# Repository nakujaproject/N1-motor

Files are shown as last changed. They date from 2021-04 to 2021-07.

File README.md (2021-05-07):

# N1-motor
`
 Reporsitory that holds files related to the N1 motor development for the Nakuja Project`

    

***
## Table of Contents

1. [Description](#description)
2. [Goals](#goals)
3. [Methodology](#methodology)
4. [Key Design Parameters](#key-design-parameters)
5. [Directories](#directories)
6. [Technologies](#technologies)

***

## Description

The N1 motor is a Solid Rocket Motor developed by the Nakuja Project. The motor is meant to be used on a small launch vehicle. The purpose of the motor is to offer propulsion to a rocket that will be recovered in so doing put into practise the skills of armature experimental rocketry

## Goals
The N1 motor is expected to propel the launch vehicle to a hieght of between `50 to  100m`

## Methodology
The motor is made up of one of three propellant combinations:
> + KNSU(Potassium Nitrate + Sucrose)
> + KNDX(Potassium Nitrate + Dextrose)
> + KNSB(Potassium Nitrate + Sorbitorl)

The three fuels are to be cast to form free standing grains which are to  be assembled in a pvc pipe along with a nozzle and endcaps.
This repo contains design, simulation data as well as results obtained from static tests conducted on different grains and parameters

## Key Design Parameters
The following factors are taken into consideration when designing the N1 motor:
- Performance- The motor must provide enough thrust to take the launch vehicle to a minimum of 50m
- Chamber Pressure - The chamber pressure must be within the workable range of the UPvc pipe we are currently using
- Rocket Airframe design-  the rocket must fit into the designed launch vehicle

## Directories
The following is a list of the contents of each directory in the reporsitory:
+ [Drawings](/Drawings) - contains all the design drawings for the N1 motor
+ [Proposed Final Spec](/Proposed%20Final%20Spec) -contains design simulations to obtain specifications for final motor
+ [Tests](/Tests) -contains all data obtained from static tests

## Technologies
The design and simulation of the N1 motor uses the following software:
1. SRM.xls obtained from the nakka rocketry website. Link attached [here](https://www.nakka-rocketry.net/soft/SRM_2014.1.zip)
2. openMotor- [Link](https://github.com/reilleya/openMotor)
3. OpenRocket - [Link](https://openrocket.info/)

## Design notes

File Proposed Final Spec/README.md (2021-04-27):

# Updated proposed N1-Motor
Grain Diameter 30mm \
Grain Length 150mm
performance | KNSU V6 | KNSU V7 | KNDX V8 | KNDX V9 
--- | --- | --- | --- | --- 
Designation | F87 | F92 | F65 | F63
Impulse | 67.07 | 66.91 | 70.37 | 72.65
Propellant mass (Kg) | 0.13 | 0.14 | 0.15 | 0.15
Average Pressure (MPa) | 1.45 | 1.80 | 1.87 | 1.83
Peak Pressure (MPa) | 1.89 | 2.40 | 2.33 | 2.31
Core (mm) | 17 | 16 | 14 | 13
Throat (mm) | 12 | 11 | 9 | 9
Burn Time (s) | 0.69 | 0.69 | 1.05 | 1.11
Rasp File | [ENG FILE](V6-KNSU/V6-KNSU.eng)| [ENG FILE](V7-KNSU/V7-KNSU.eng)| [ENG FILE](V8-KNDX/V8-KNDX.eng)| [ENG FILE](V8-KNDX/V8-KNDX.eng)
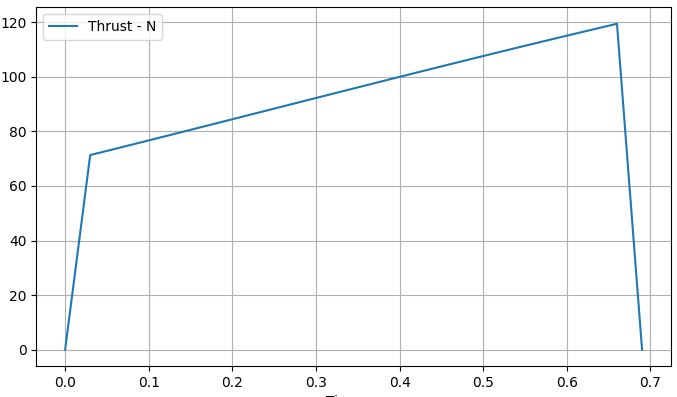
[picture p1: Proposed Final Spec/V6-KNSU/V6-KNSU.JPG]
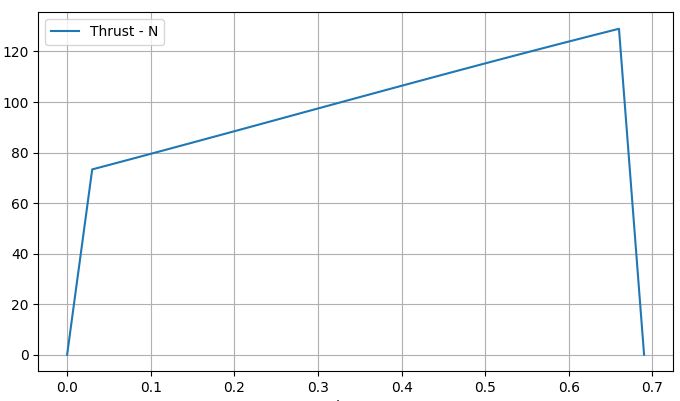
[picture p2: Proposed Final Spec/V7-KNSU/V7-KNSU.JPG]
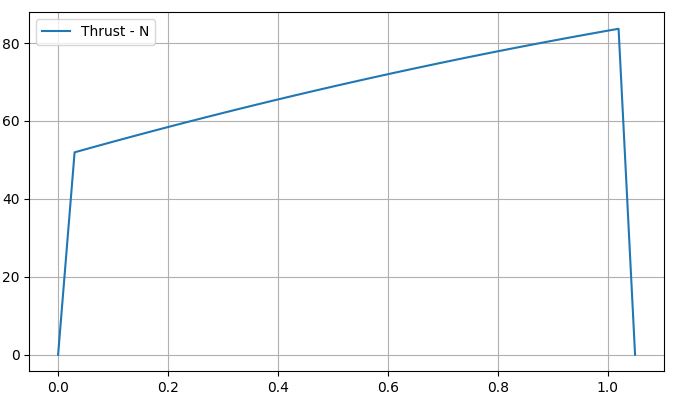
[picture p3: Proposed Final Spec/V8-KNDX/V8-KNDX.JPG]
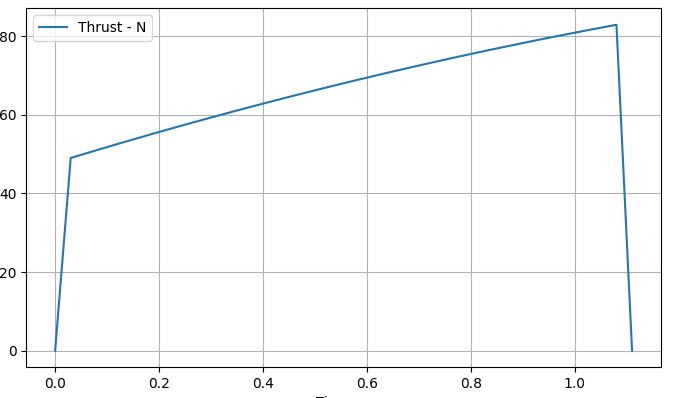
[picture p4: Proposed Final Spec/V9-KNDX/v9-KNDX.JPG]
Thrust Curve |  |  |  | 

# Motor selection
https://docs.google.com/spreadsheets/d/1xEjgxcizVEla5WYd4yQHLdHGN3GgNQR9PQ9QDNRd-24/edit?pli=1#gid=1338705104

# New motor specifications with nozzles

Grain Diameter 30mm \
Grain Length 130mm

performance | KNSU v10 | KNDX v11 | KNSB v12
--- | --- | --- | ---
Designation | G146 | G106 | G108
Impulse(Ns) | 109.61 | 115.36 | 110.36
Propellant mass (Kg) | 0.12 | 0.13 | 0.13
Average Pressure (MPa) | 1.46 | 1.46 | 1.48
Peak Pressure (MPa) | 1.89 | 1.79 | 1.79
Core (mm) | 16 | 14 | 14
Throat (mm) | 11 | 9.5 | 9.5
Burn Time (s) | 0.72 | 1.05 | 0.99
Rasp File | [ENG FILE](V10-KNSU/N1-V10-KNSU.eng) | [ENG FILE](V11-KNDX/N1-V11-KNDX.eng) | [ENG FILE](V12-KNSB/N1-V12-KNSB.eng)
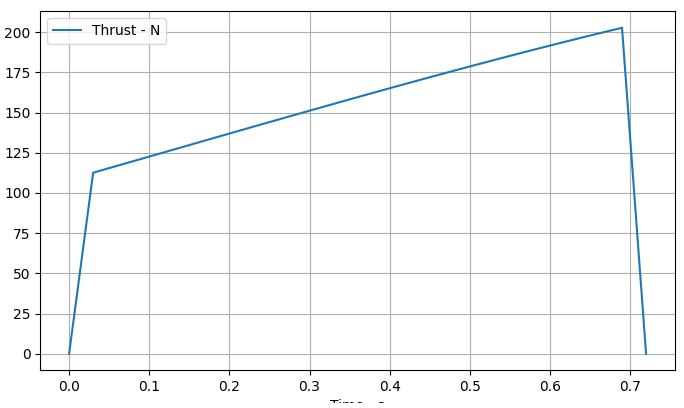
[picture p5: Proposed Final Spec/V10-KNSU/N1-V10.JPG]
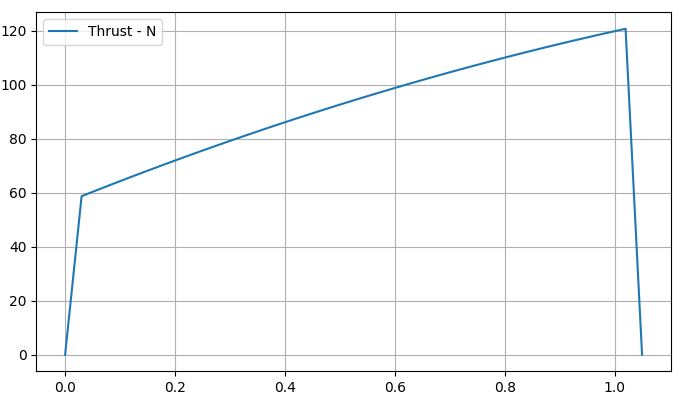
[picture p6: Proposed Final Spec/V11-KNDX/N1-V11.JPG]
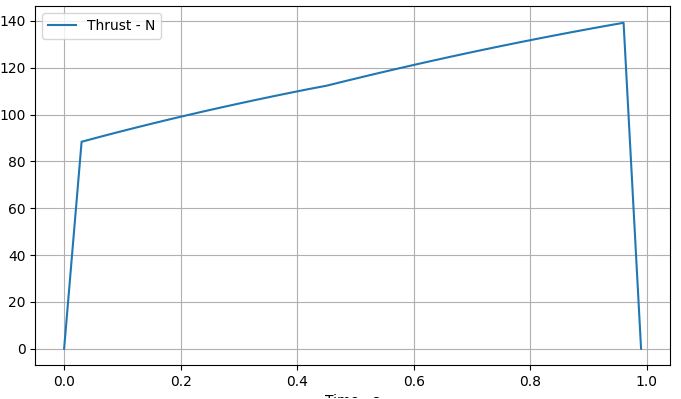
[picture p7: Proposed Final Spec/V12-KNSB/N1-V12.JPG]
Thrust Curve |  |  |

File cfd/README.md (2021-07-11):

# N1 Nozzle CFD
### Pressure
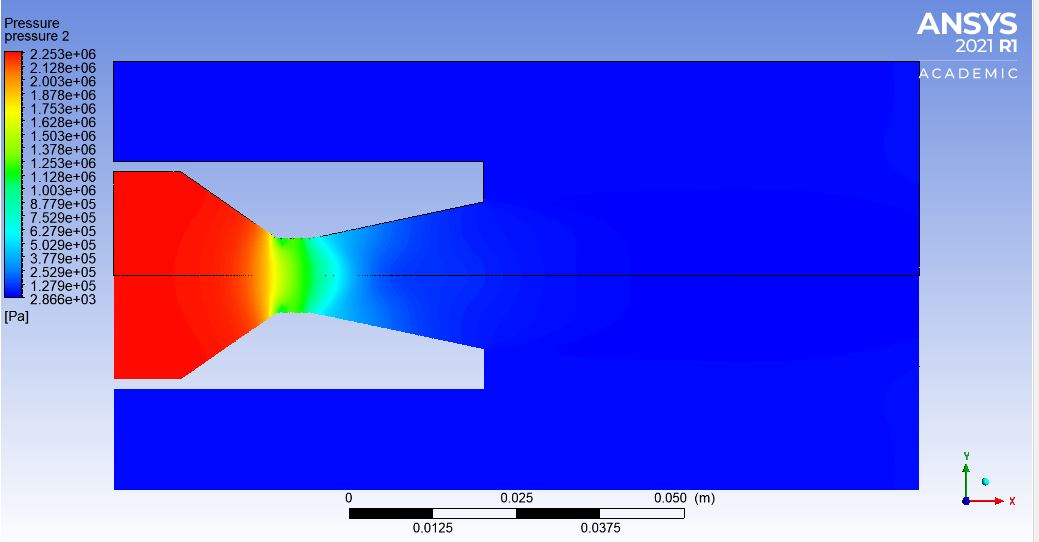
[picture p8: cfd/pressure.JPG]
 
### Mach number
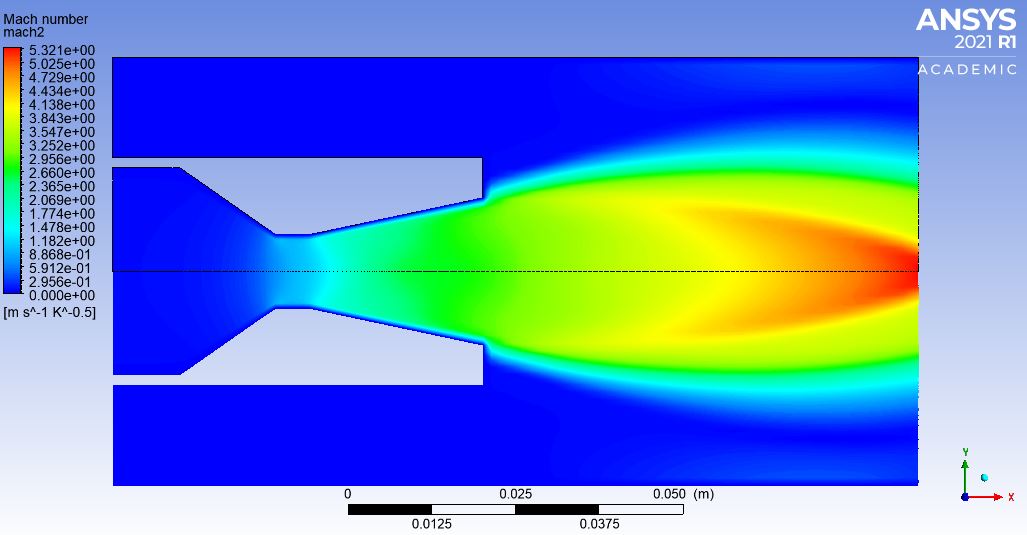
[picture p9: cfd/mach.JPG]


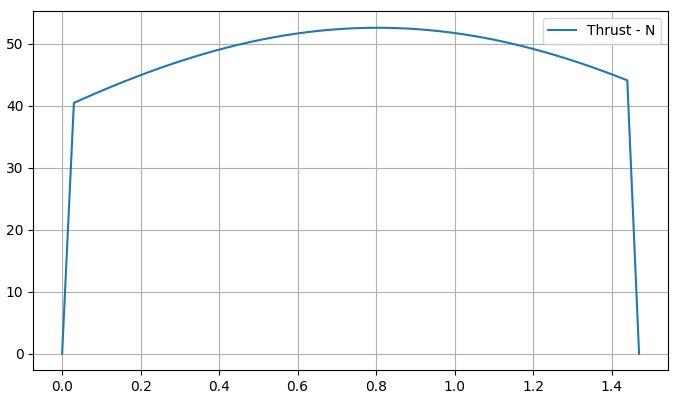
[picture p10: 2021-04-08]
Proposed Final Spec/N1-KNSU-proposed/KNSU.JPG

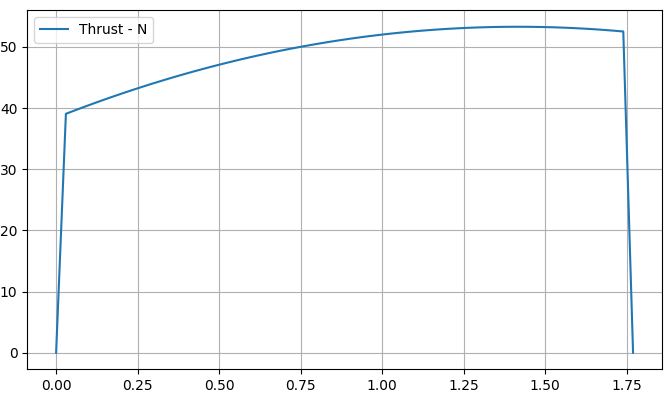
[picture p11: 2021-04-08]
Proposed Final Spec/N1-KNDX-proposed/KNDX.JPG

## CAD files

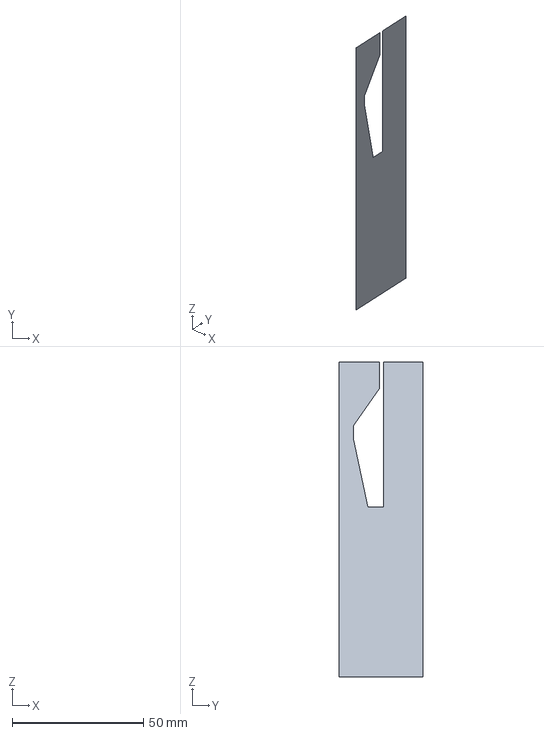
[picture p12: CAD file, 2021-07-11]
cfd/n1-nozzle.stp
0 x 32.0 x 120.0 mm

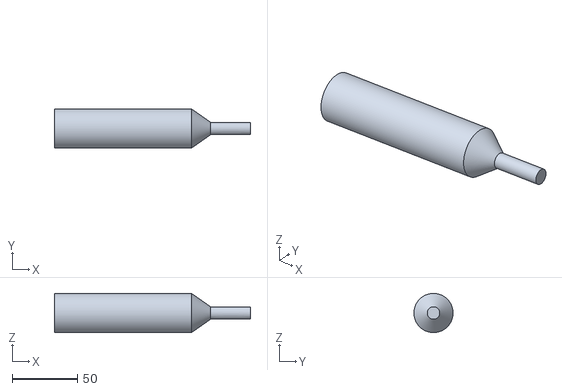
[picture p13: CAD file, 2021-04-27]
Drawings/nozzle design/nozzle mould tool kndx.stl
150.0 x 30.0 x 30.0

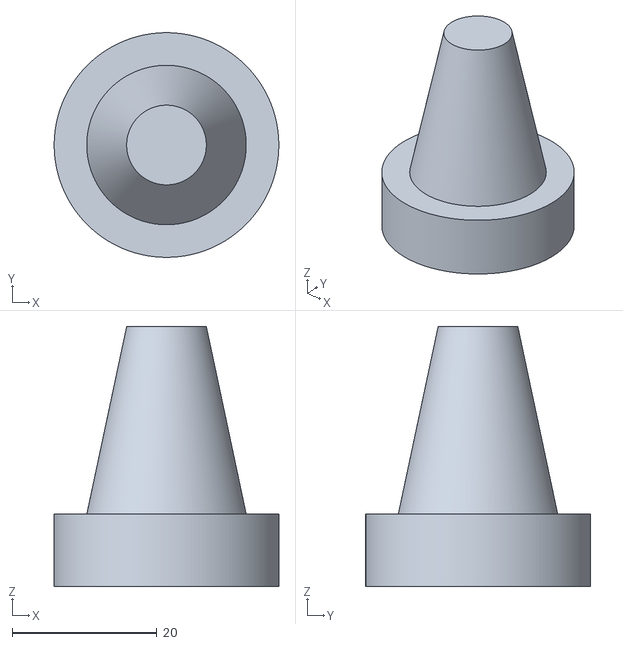
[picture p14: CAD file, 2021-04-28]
Drawings/Part1.stl
31.0 x 31.0 x 35.9

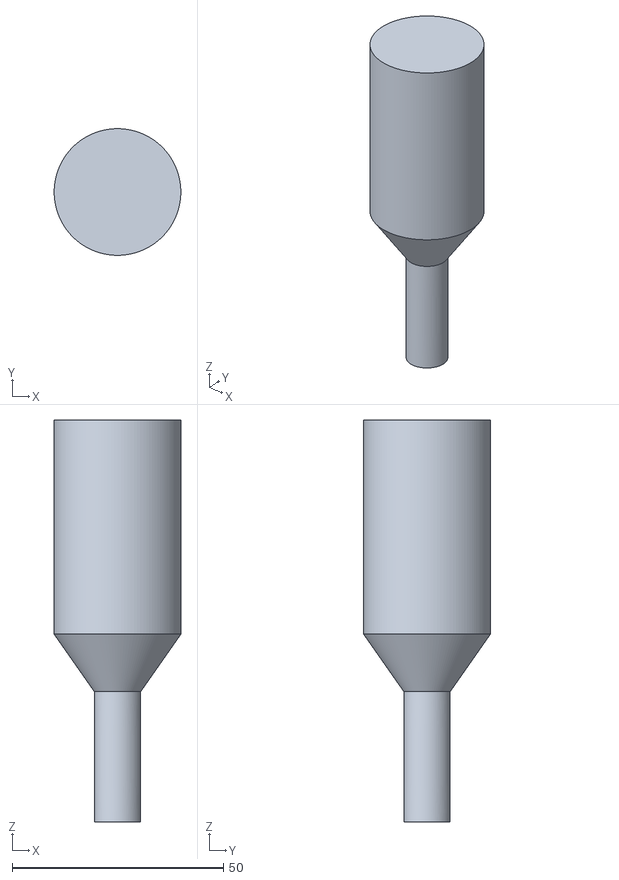
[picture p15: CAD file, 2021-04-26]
Drawings/nozzle design/nozzle mould tool top.stl
30.0 x 30.0 x 95.2

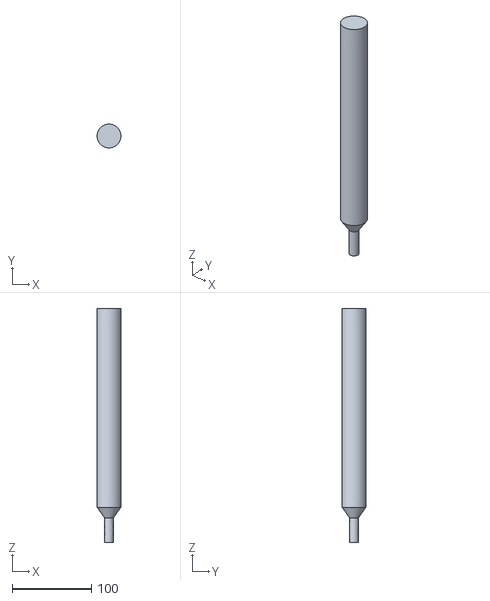
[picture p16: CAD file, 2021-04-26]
Drawings/nozzle design/nozzle mould tool.stl
30.0 x 30.0 x 295.2

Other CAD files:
Drawings/Assembly1-1.idw
Drawings/Assembly1.iam
Drawings/OldVersions/endcap.0002.ipt
Drawings/OldVersions/grain.0001.ipt
Drawings/bulkhead.ipt
Drawings/casing.ipt
Drawings/endcap.ipt
Drawings/grain.ipt
Drawings/insulation.ipt
Drawings/nozzle design/OldVersions/nozzle mould tool.0001.ipt
Drawings/nozzle design/nozzle mould tool kndx.ipt
Drawings/nozzle design/nozzle mould tool.ipt
Drawings/nozzle design/optimum nozzle.ipt
Drawings/nozzle.ipt

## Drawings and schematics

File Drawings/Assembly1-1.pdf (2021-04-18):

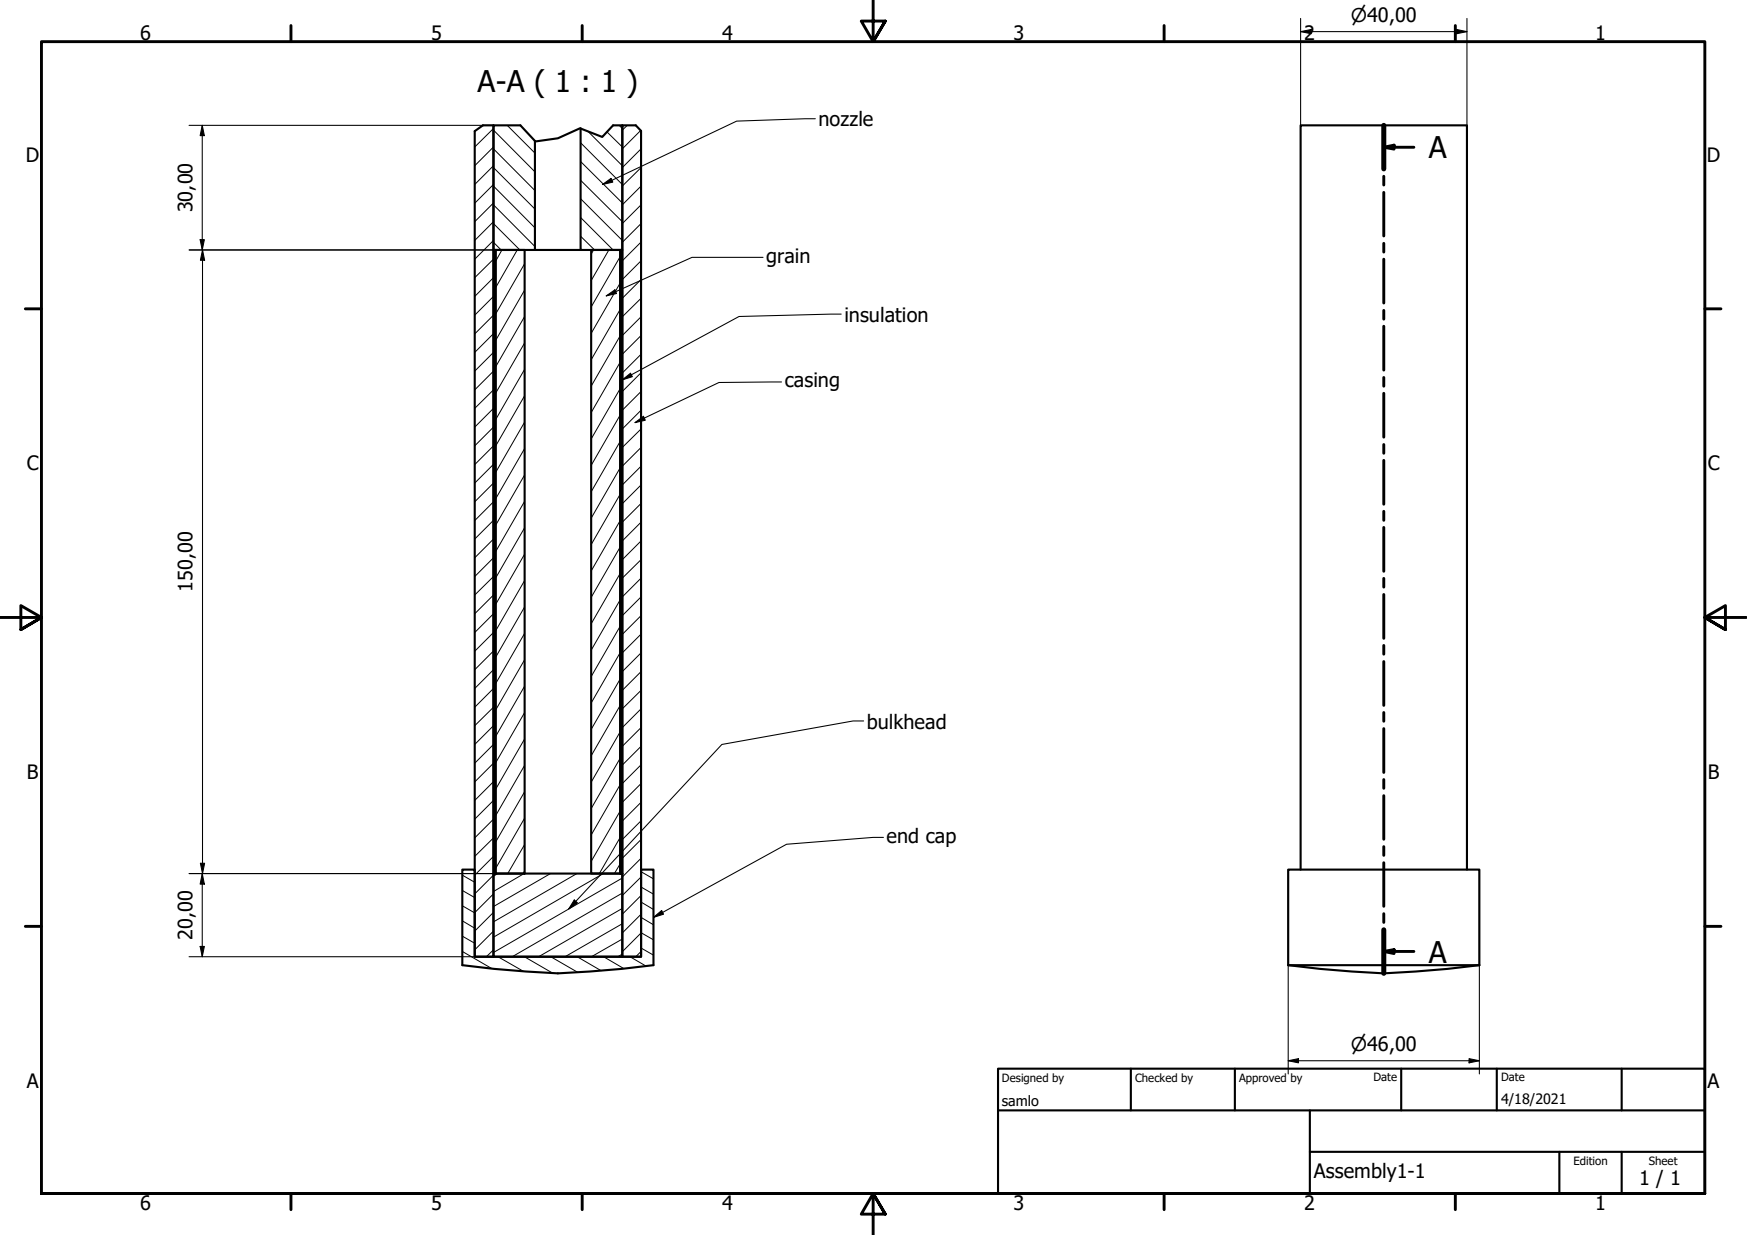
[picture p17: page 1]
Designed by; Checked by; Approved by; Date; end cap

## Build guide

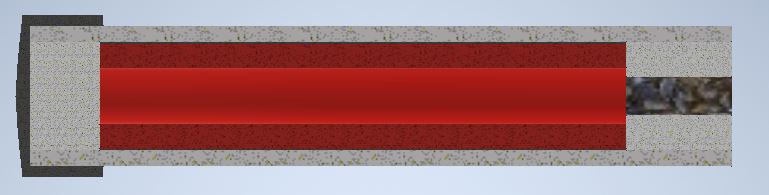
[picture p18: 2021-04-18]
Drawings/assembly.JPG

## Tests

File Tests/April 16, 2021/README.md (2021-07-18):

#N1 - Test motors

[Youtube video](https://www.youtube.com/watch?v=pPzbUa3gl14)\
[Blog](https://nakujaproject.blogspot.com/2021/04/static-firing-test-report-16th-april.html)

Details |V6 | V7 
--- | --- | --- 
Total Impulse (N-s)| 28.07 | 23.50 
Specific Impulse (N-s/Kg) | 155.94 | 156.68
Average Thrust (N) | 23.39 | 19.58 
Peak Thrust (N) | 32 | 51
Motor Class| E | E
Fuel | Sucrose | Sucrose 
Rasp File | [File](n1-v6.eng) | [File](n1-v7.eng) 
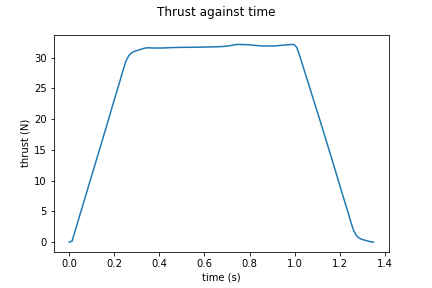
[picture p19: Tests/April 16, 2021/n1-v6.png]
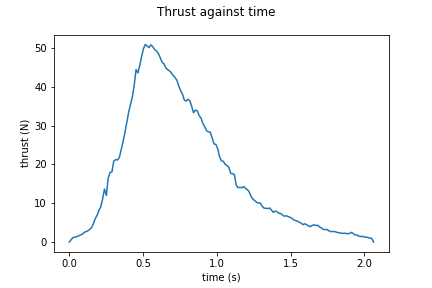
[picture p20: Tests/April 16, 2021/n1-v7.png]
Thrust Curve |  |

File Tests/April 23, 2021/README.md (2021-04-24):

# N1 - Test motors

Details |V7-control | V7-nozzle
--- | --- | --- 
Total Impulse (N-s)| 21.40 | N/A 
Specific Impulse (N-s/Kg) | 152.88 | N/A
Average Thrust (N) | 21.40 | N/A 
Peak Thrust (N) | 216.801 | N/A
Motor Class| E | N/A
Fuel | Sucrose | Sucrose 
Rasp File | [File](v7-control.eng) | N/A
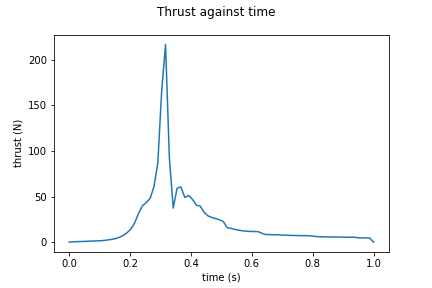
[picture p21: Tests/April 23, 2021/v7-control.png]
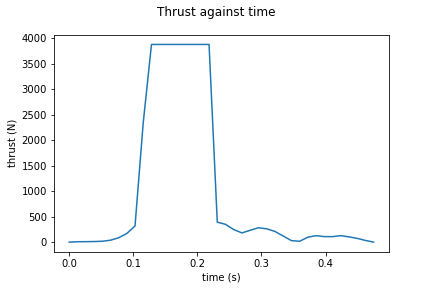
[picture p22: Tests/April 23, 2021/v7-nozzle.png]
Thrust Curve |  | 

## Notes
The control version had a failure on the nozzle but some data was still collected.
The failure of the nozzle might have resulted from shortcomings in the nozzle construction or rapid increase in chamber pressure above the design parameters of the nozzle. \
The nozzle version had a catastrophic failure resulting in the loss of the test stand. 
The data gathered was not useful as it exceeds the measurable limit of the load cells as well as the test stand being destroyed.

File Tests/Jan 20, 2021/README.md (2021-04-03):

#N1 - Test motors

Details |Motor 1 | Motor 2 | Motor 3
--- | --- | --- | ---
Total Impulse| 0.22 | 0.05 | 0.12
Specific Impulse| 14.57 | 3.29 | 8.2
Average Thrust| 0.38 | 0.18 | 0.23
Motor Class| micro | micro | micro 
Fuel | Sucrose | Dextrose | Sucrose
Rasp File | [File](n1-t1-m1.eng) | [File](n1-t1-m2.eng) | [File](n1-t1-m3.eng)
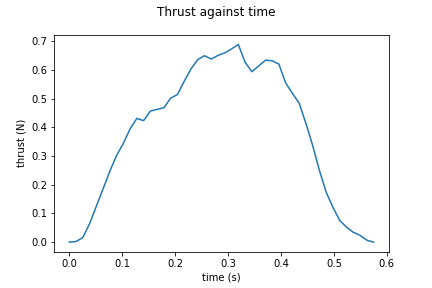
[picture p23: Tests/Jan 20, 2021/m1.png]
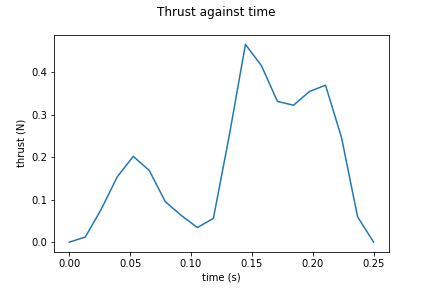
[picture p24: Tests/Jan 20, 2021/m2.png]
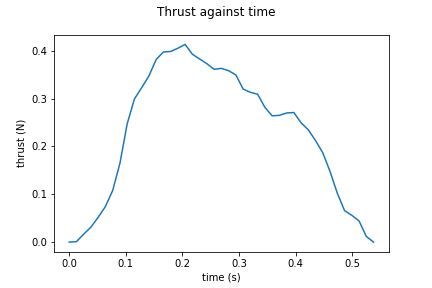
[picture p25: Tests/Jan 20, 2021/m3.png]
Thrust Curve |  |  |

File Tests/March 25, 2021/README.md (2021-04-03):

# N1 - Spec 1

## Report
 - [blog](https://nakujaproject.blogspot.com/2021/03/static-firing-test-report-25th-march.html)

## Thrust Curve
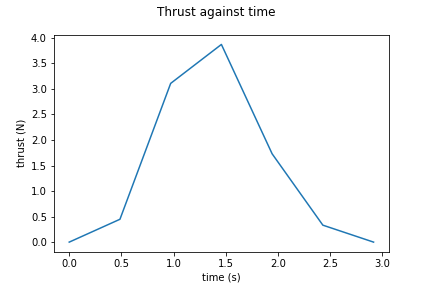
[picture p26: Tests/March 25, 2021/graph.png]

## Rasp File
- [eng file](n1-sp1.eng)

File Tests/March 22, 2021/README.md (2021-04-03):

# N1 - T2

## Report
- [blog](https://nakujaproject.blogspot.com/2021/03/report-on-static-testing-done-on-22-nd.html)

## State
Failed

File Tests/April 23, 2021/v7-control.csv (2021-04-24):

-2.579439252336312549e+00
-2.252336448597994867e+00
3.644859813085472577e-01
3.635514018691725191e+00
9.102803738317893689e+00
1.447663551401882920e+01
1.704672897196275372e+01
1.872897196261695996e+01
1.737383177570107051e+01
2.036448598130854748e+01
2.503738317757023069e+01
2.798130841121509249e+01
2.625233644859826754e+01
2.858878504672911092e+01
3.340186915887863961e+01
3.055140186915901523e+01
3.344859813084126188e+01
3.541121495327116975e+01
3.858878504672910736e+01
3.947663551401883097e+01
4.335514018691602445e+01
4.171962616822443692e+01
3.975700934579452905e+01
3.924299065420574806e+01
3.863551401869172963e+01
3.928971962616836322e+01
3.994392523364499681e+01
4.120560747663565593e+01
4.260747663551416053e+01
4.704672897196275727e+01
4.167289719626182176e+01
4.073831775700948299e+01
4.494392523364499681e+01
4.045794392523378491e+01
4.653271028037396917e+01
5.966355140186929873e+01
5.298130841121509604e+01
3.069158878504686783e+01
3.728037383177584019e+01
3.999065420560761197e+01
4.237383177570107051e+01
3.536448598130854748e+01
3.157943925233658788e+01
2.886915887850481255e+01
3.171962616822443692e+01
3.503738317757023424e+01
4.111214953271041850e+01
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

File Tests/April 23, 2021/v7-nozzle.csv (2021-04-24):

3.464330218068535032e+02
3.393302180685357143e+02
3.359657320872273090e+02
3.336292834890965082e+02
3.267601246105917880e+02
3.238161993769469404e+02
3.274143302180684714e+02
3.284423676012460191e+02
3.308722741433020929e+02
3.262928348909656506e+02
3.242367601246104982e+02
3.245638629283488399e+02
3.263395638629282303e+02
3.191433021806852821e+02
3.174610591900310510e+02
3.206386292834890241e+02
3.209190031152647293e+02
3.178816199376946088e+02
3.117133956386292084e+02
3.123208722741431984e+02
3.145171339563862034e+02
3.197975077881619086e+02
3.211526479750777980e+02
3.178348909657319723e+02
3.173676012461058349e+02
3.215264797507787193e+02
3.195171339563862034e+02
3.200778816199376138e+02
3.214797507788160829e+02
3.235825545171338717e+02
3.170872274143301297e+02
3.164797507788160829e+02
3.176012461059189036e+02
3.182087227414329504e+02
3.209657320872273090e+02
3.229750778816198249e+02
3.248909657320871247e+02
3.224143302180684714e+02
3.229750778816198249e+02
3.276479750778815401e+02
3.270872274143301297e+02
3.212461059190030142e+02
3.207320872274142403e+02
3.261993769470404345e+02
3.221806853582553458e+02
3.207788161993768767e+02
3.249844236760123977e+02
3.320404984423674932e+02
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

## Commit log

2021-04-03 Raw data
    [Monday 22 March 2021 12-36PM.csv, Thursday 25 March 2021 01-47PM.csv, naKUJA-MOTOR3-TEST4.CSV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]
2021-04-08 cleaning up
    [Tuesday 06 April 2021 12-49PM (1).csv, Tuesday 06 April 2021 12-49PM.csv]
2021-04-12 :sparkles: New motor data
    new motor for simulation
2021-04-13 :sparkles: New motor data
    New motor eng file
2021-04-13 :memo: Motor documentation
    Adding documentation for motor .eng files
2021-04-13 :ambulance: Fixing calculation error
    fixing calculation error in motor mass
2021-04-13 updated test motor test spec motors
2021-04-14 :sparkles: added .ric, .eng and .ork files
    added simulatiom files for proposed motors
2021-04-14 motor mass calculations
2021-04-16 April 6th tests
    Files and description, and mini analysis
    [V7-raw.csv, v6-raw.csv, v6.csv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]
2021-04-18 Drawings and illustrations
    [Assembly1-1.idw, Assembly1.iam, bulkhead.ipt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]
2021-04-24 April 23, 2021 Test
    [v7-control.csv, v7-nozzle.csv]
2021-04-26 :sparkles: nozzle drawings
    drawings for nozzle fabrication
    [nozzle mould tool.ipt, optimum nozzle.ipt]
2021-04-26 Add printables
    [nozzle mould tool top.stl, nozzle mould tool.0001.ipt, nozzle mould tool.ipt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]
2021-04-27 KNDX mould tool
    [nozzle mould tool kndx.ipt, nozzle mould tool kndx.stl]
2021-04-27 Updated N1 with nozzle motors
2021-04-27 adding sorbitol motor v12
2021-07-11 n1 nozzle cfd
    [n1-nozzle.stp]
2021-07-18 prop mass
